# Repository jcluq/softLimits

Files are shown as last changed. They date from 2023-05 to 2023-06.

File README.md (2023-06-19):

# Elipses

Elipses are a series of kinetic sculptures which base their design on a string loop throwing contraption referred to as a string shooter. The mechanism consists of two motors rotating in opposite directions, which impulse a loop of yarn to a distance dependent on the speed of the motors and the length of the string. Because the string is looped, the yarn returns to the string shooter, getting fed again into the motors. This continuous throw generates a levitating elliptical shape. This phenomenon is quite interesting and eye-catching, as it produces a peculiar behavior that our perception is not used to experiencing.

## softLimits

On softLimits, 5 different nodes are located in the space close to eachother. Each node consists of a string shooter mounted on a servo motor to control the angle of throw. The servo motor is then mounted on top of a rotating platform controlled by a stepper motor. A slip ring is used to connect the servo motor and allow 360+ degrees of rotation without entangling the cables. All the motors are driven by a ESP32 based micro controller which rests on a custom PCB for handling all the copper circuitry.

The esp32 micro controller on each node allows them to do be controlled via Wi-Fi through OSC messages using UDP protocol. A custom software made in Processing acts as an interface for the nodes, allowing real time visualization of position and speed, as well as sending messages to them in order to change their parameters.

For the Soft Limits choreography, each node has a behaviour assigned to it. Behaviors are made up of 4 different parameters: throwing speed, rotation speed, rotation direction, and shooter angle. The nodes are then allowed to run on these parameters freely, until the software detects a collision between them. When this happens, a "swap" between parameters occurs, changing the shapes and movement of both nodes. When the 5 nodes are allowed to run freely and interact, an ever-changing play takes place.

## PoC (Process of Creation)

The creation of this artwork has meant a multidisciplinary research touching a number of different disciplines: wireless communications, mechanical design, digital fabrication, circuit and PCB design, welding, among many others. 

For the first string shooters I was basing myself on a design created by the user scorch on the page [Thingy verse](https://www.thingiverse.com/thing:3647986). This version was almost entirely made of laser cut parts, which even tho they where quick to produce, they were also very difficult to modify mainly because I didnt had the original archives that were used to design the devices. 

My next step was to create my own string shooter. For this I 3D modeled my own parts with the use of TICAD and start 3d printing the parts. This allowed me to test and modify specific parts and functions in a relative cheap and fast way. I changed the 5VDC motors I was using for faster and stronger 5-24V motors. The hardest obstacle I kept on finding was the lack of friction on the wheels which made contact with the yarn. On a [research](https://www.researchgate.net/publication/338578099_String_Shooter's_overall_shape_in_ambient_air) about the overall shapes of string shooters in air, the use of RC cars wheels was reported successful. After implementing these wheels on my design, I achieved a desired stability on my string shooters. 

For the tilt and pan module, I used a mg996r motor attached to a tilt metal bracket. Due to the screw fixtures on the bracket, setting up the string shooter on top of it was very easily done, by using threaded inserts on the 3d printed material. For the pan mechanism, I designed a tower structure to hold the bearings and the slip ring together, while giving enough space for the tilt mechanism to change angle without obstruction. For all this design process, fusion360 was very useful again as it allowed me to design with a modular a approach, having different parts which would then be "assembled" onto the final object. This modular approach proved to be a great constrain to prototyping because of the constant tests and modifications. 

For the electrical and communication design, I wanted to have a single line of power as the only physical input to each node. I used 12V as my main power and later used a LM1085 power regulator to send 5V to both my servomotor and micro controller. The ESP32 drive the 24VDC motors through an IRL540 mosfet, using PWM to change the throwing speed. The esp uses an A4988 driver in order to translate the stepper movements as well as to set up micro stepping. The mg996r motor is driven simply by a PWM output. 

The PCB was designed in KiCad and its shape and design was made to fit on the previous 3D models designed on Fusion360.

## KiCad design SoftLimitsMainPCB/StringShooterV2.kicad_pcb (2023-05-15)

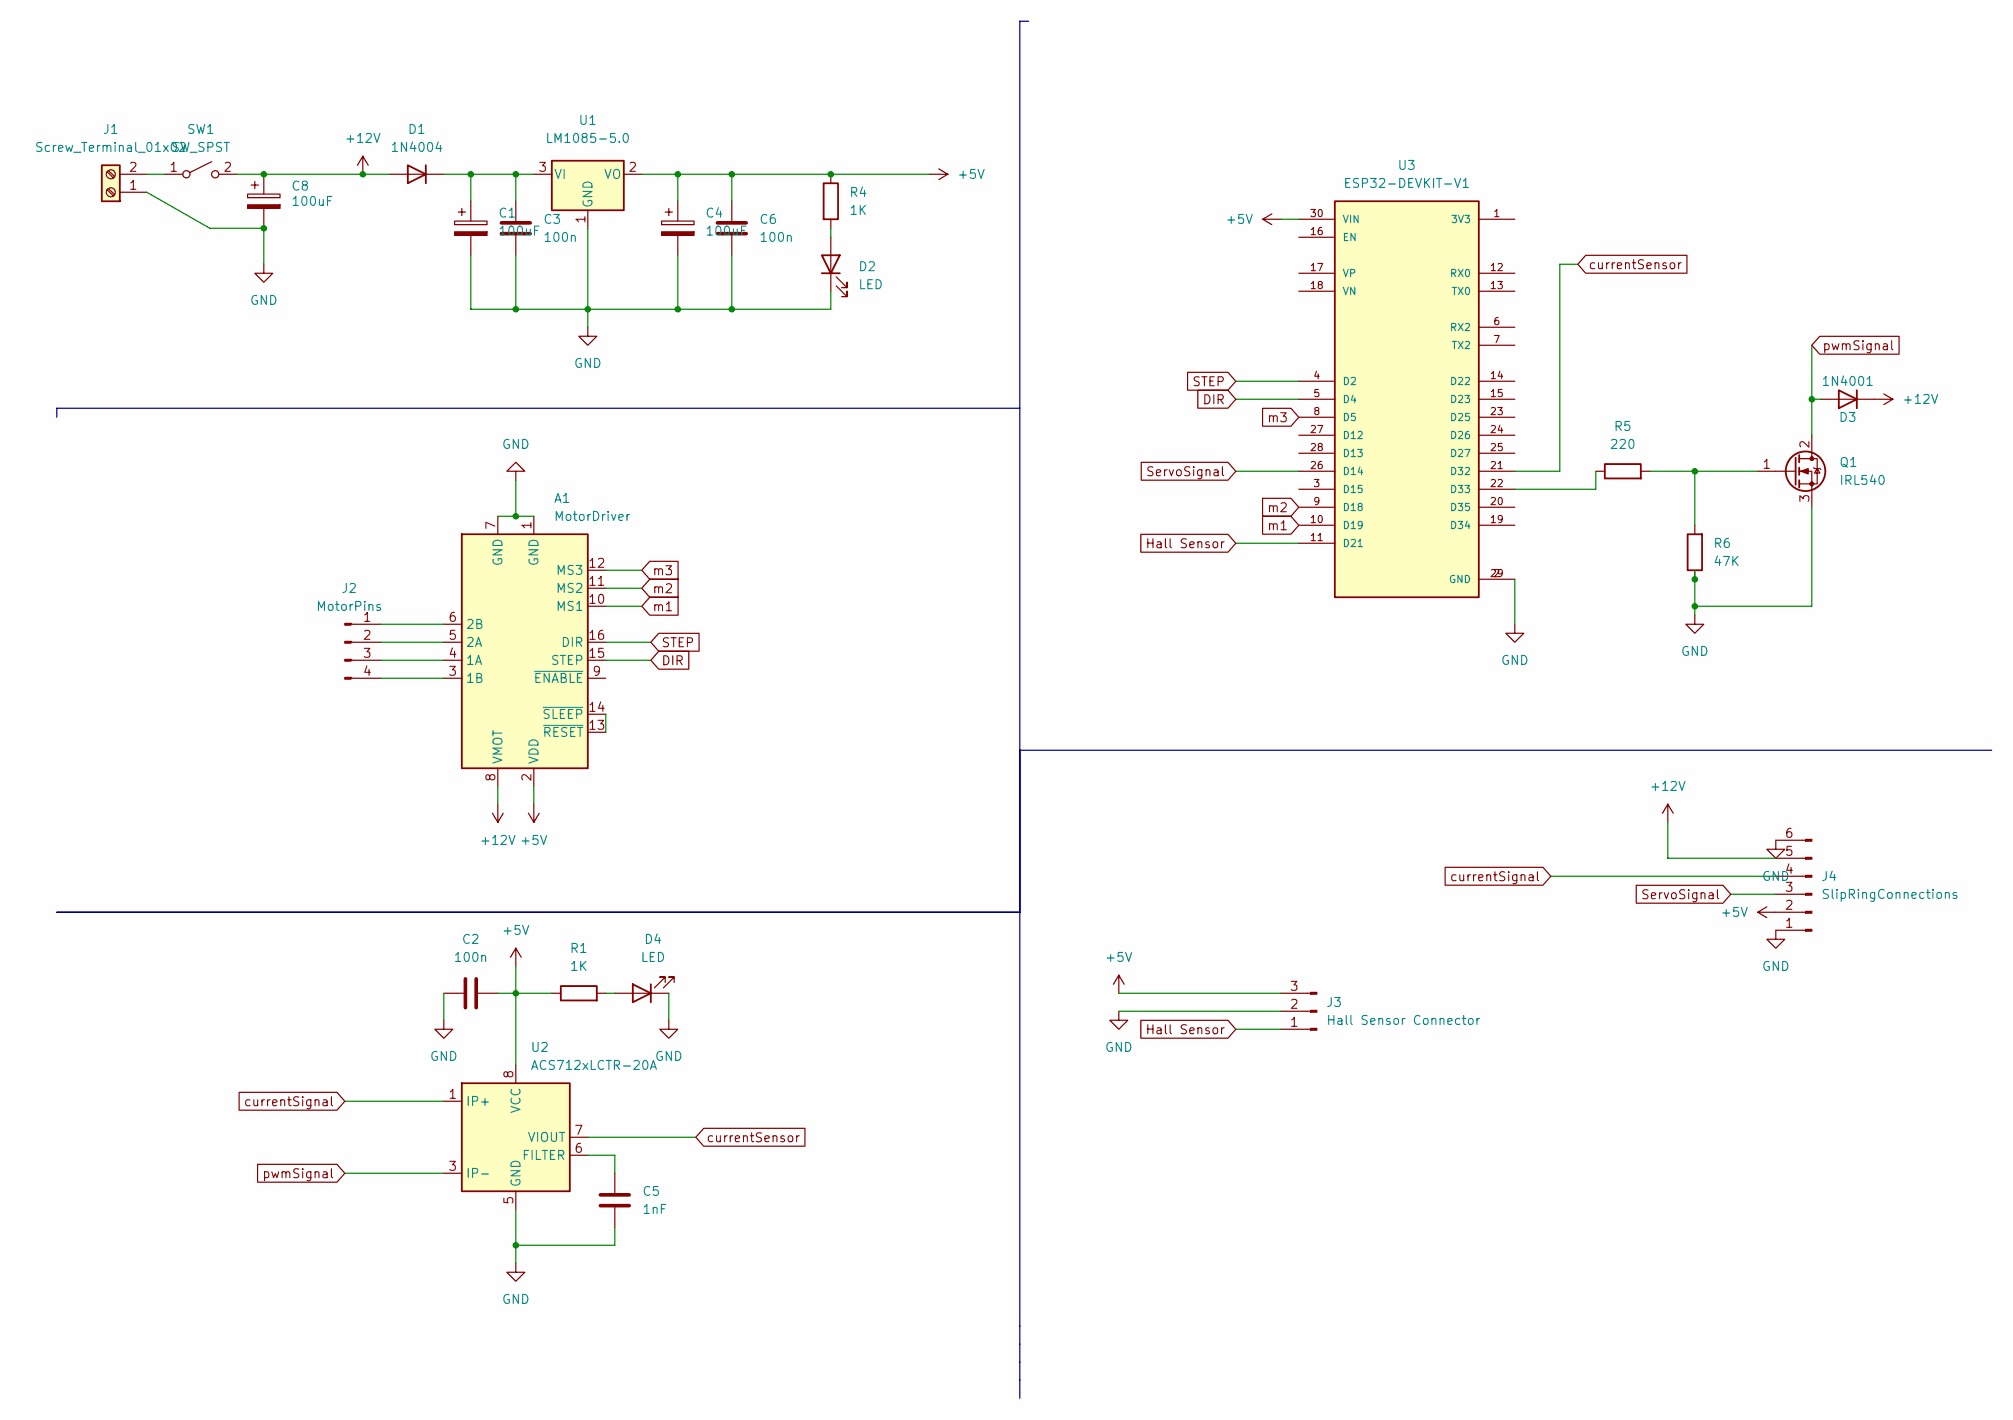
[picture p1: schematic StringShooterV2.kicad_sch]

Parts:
A1: MotorDriver; Pololu_Breakout-16_15.2x20.3mm
C1, C4, C8: 100uF; CP_Radial_D6.3mm_P2.50mm
C2, C3, C6: 100n; C_0805_2012Metric_Pad1.18x1.45mm_HandSolder
C5: 1nF; C_0805_2012Metric_Pad1.18x1.45mm_HandSolder
D1: 1N4004; D_SMA_Handsoldering
D2, D4: LED; D_0603_1608Metric_Pad1.05x0.95mm_HandSolder
D3: 1N4001; D_SMA_Handsoldering
J1: Screw_Terminal_01x02; TerminalBlock_bornier-2_P5.08mm
J2: MotorPins; PinSocket_1x04_P2.54mm_Vertical
J3: Hall Sensor Connector; PinSocket_1x03_P2.54mm_Vertical
J4: SlipRingConnections; PinSocket_1x06_P2.54mm_Vertical
Q1: IRL540; TO-220-3_Horizontal_TabDown
R1, R4: 1K; R_0805_2012Metric_Pad1.20x1.40mm_HandSolder
R5: 220; R_0805_2012Metric_Pad1.20x1.40mm_HandSolder
R6: 47K; R_0805_2012Metric_Pad1.20x1.40mm_HandSolder
SW1: SW_SPST; mts102
U1: LM1085-5.0; TO-263-3_TabPin2
U2: ACS712xLCTR-20A; SOIC-8_3.9x4.9mm_P1.27mm
U3: ESP32-DEVKIT-V1; MODULE_ESP32_DEVKIT_V1; PARTREV N/A

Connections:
+5V: A1.2 (VDD), C2.2, C4.1, C6.1, J3.3, J4.2, R1.1, R4.1, U1.2 (VO), U2.8 (VCC), U3.30 (VIN)
+12V: A1.8 (VMOT), C8.1, D1.2 (A), D3.1 (K), J4.5, SW1.2 (B)
DIR: A1.15 (STEP), U3.5 (D4)
GND: A1.1 (GND), A1.7 (GND), C1.2, C2.1, C3.2, C4.2, C5.2, C6.2, C8.2, D2.1 (K), D4.1 (K), J1.1, J3.2, J4.1, J4.6, Q1.3 (S), R6.1, U1.1 (GND), U2.5 (GND), U3.2 (GND), U3.29 (GND)
Hall Sensor: J3.1, U3.11 (D21)
unnamed: A1.3 (1B), J2.4
unnamed: A1.4 (1A), J2.3
unnamed: A1.5 (2A), J2.2
unnamed: A1.6 (2B), J2.1
unnamed: A1.13 (~RESET), A1.14 (~SLEEP)
unnamed: C1.1, C3.1, D1.1 (K), U1.3 (VI)
unnamed: C5.1, U2.6 (FILTER)
unnamed: D2.2 (A), R4.2
unnamed: D4.2 (A), R1.2
unnamed: J1.2, SW1.1 (A)
unnamed: Q1.1 (G), R5.2, R6.2
unnamed: R5.1, U3.22 (D33)
STEP: A1.16 (DIR), U3.4 (D2)
ServoSignal: J4.3, U3.26 (D14)
currentSensor: U2.7 (VIOUT), U3.21 (D32)
currentSignal: J4.4, U2.1 (IP+), U2.2 (IP+)
m1: A1.10 (MS1), U3.10 (D19)
m2: A1.11 (MS2), U3.9 (D18)
m3: A1.12 (MS3), U3.8 (D5)
pwmSignal: D3.2 (A), Q1.2 (D), U2.3 (IP-), U2.4 (IP-)

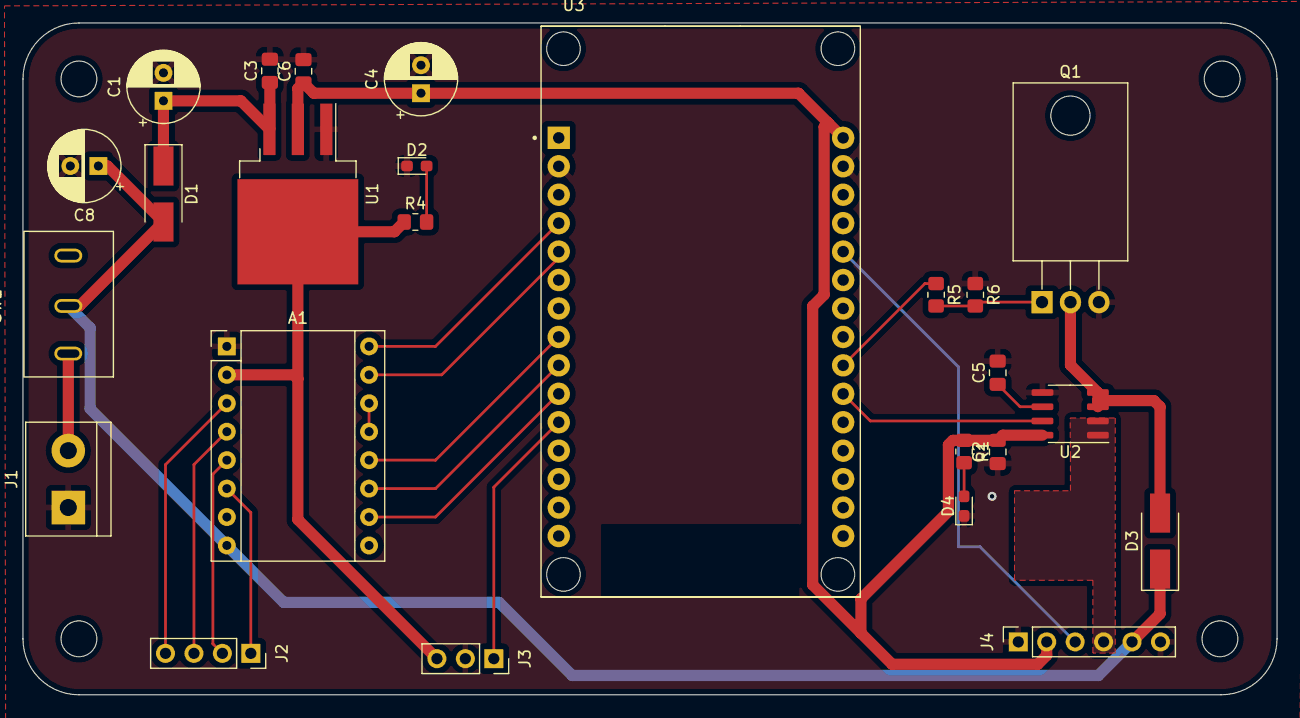
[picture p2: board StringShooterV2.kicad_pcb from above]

Board: 2 copper layers, 112.0 x 60.0 mm, 25 parts (0 on the bottom side), 25 nets.

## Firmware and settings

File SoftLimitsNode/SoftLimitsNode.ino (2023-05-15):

/*
   StringNode
    
   Code based in ralfs beacker boilerplate  
   https://github.com/rlfbckr/simple-node

*/

#include <ESP32Servo.h>
#include <WiFi.h>
#include <WiFiMulti.h>
#include <HTTPClient.h>
#include <HTTPUpdate.h>
#include "AsyncUDP.h"
#include "Shooter.h"


#include <Chrono.h>
#include <OSCBundle.h>
#include <EEPROM.h>
#include <AccelStepper.h>

#define EEPROM_SIZE 12
#define DIR_PIN 2
#define STEP_PIN 4
#define SH_PIN 33
#define M1_PIN 19
#define M2_PIN 18
#define M3_PIN 5
#define HOME_PIN 21
#define SERVO_PIN 14
#define CUR_PIN 32


int MY_NODE_ID = -1;

float FW_VERSION = 0.17; /// increment for next upload



//const char DEFAULT_URL_FW_VERSION[] = "http://192.168.0.113:8080/release/version.txt";
//const char  DEFAULT_URL_FW_BINARY[] = "http://192.168.0.113:8080/release/firmware.bin";

const char DEFAULT_URL_FW_VERSION[] = "http://192.168.4.100:8080/release/version.txt";
const char  DEFAULT_URL_FW_BINARY[] = "http://192.168.4.100:8080/release/firmware.bin";

boolean LOCK_UDP_REICEIVER = false; // lock UDP/OSC receiver to avoid shit while flashing a new firmware
char URL_FW_VERSION[512];
char URL_FW_BINARY[512];
boolean UPDATE_FIRMWARE = false; // hook in firmwareupdate

long pingInterval = 5; // every 2 seconds
int networkLocalPort = 8888;
int networkOutPort = 9999; // remote port to receive OSC

int stepNum = 500;
int microStep = 16;
int jogVal = 2000000;
int stepperSpeed = 10 * microStep;
int stepperDirection = 1;
int stepperRealPosition;

boolean HALL_SENSOR = false;
boolean isJogging = false;
int shooterSpeed = 450;

boolean HOMING = false;
boolean homingSet = false;
boolean stopper = false;



WiFiMulti wifiMulti;
Chrono pingTimer;
AsyncUDP udp;
AsyncUDP udpOut;
AccelStepper stepper(AccelStepper::DRIVER, STEP_PIN, DIR_PIN);
Servo servo;
Shooter shooter(SH_PIN);

void setup() {
  strncpy(URL_FW_VERSION, DEFAULT_URL_FW_VERSION, strlen(DEFAULT_URL_FW_VERSION));
  strncpy(URL_FW_BINARY, DEFAULT_URL_FW_BINARY, strlen(DEFAULT_URL_FW_BINARY));
  MY_NODE_ID = readNodeIDfromEEPROM();
  Serial.begin(115200);
  Serial.print("--> NODE  v:");
  Serial.println(FW_VERSION);
  initWIFI();
  initUDP();
  microStepSetup();
  
  servo.attach(SERVO_PIN);
  stepper.setMaxSpeed(1500);
  stepper.setCurrentPosition(0);
  stepper.setSpeed(stepperSpeed* stepperDirection*microStep);
  stepper.stop();

  servo.write(90);
  beginHomming();
  
}

void loop() {
  Serial.println(digitalRead(HOME_PIN));
  if (UPDATE_FIRMWARE) {
    if (getFirmwareVersionFromServer()) { // check if a new version is avaiable on the server
      updateFirmwareFromServer(); // get binary and flash it.
    }
    UPDATE_FIRMWARE = false; // update done
  }

  if (pingTimer.hasPassed(pingInterval)) {
    pingTimer.restart();
    sendPingOSC();
  }

  if (HOMING) {
    homingSequence();
      
    }
    
    


 // Serial.println(digitalRead(HOME_PIN));
 if(stopper){
  stepper.stop();
 }
 else {
  stepper.runSpeedToPosition();
 }
 //currentMeasurement();
  stepperRealPosition = (((stepper.currentPosition()/microStep)%stepNum)+stepNum)%stepNum;
  //stepper.setCurrentPosition(stepperRealPosition);
  shooter.runShooter(shooterSpeed);
  //Serial.println(((stepper.currentPosition()%stepNum)+stepNum)%stepNum);
}

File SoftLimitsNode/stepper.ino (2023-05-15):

void microStepSetup()
{
  pinMode(M1_PIN,OUTPUT);
  pinMode(M2_PIN,OUTPUT);
  pinMode(M3_PIN,OUTPUT);

  digitalWrite(M1_PIN,HIGH);
  digitalWrite(M2_PIN,HIGH);
  digitalWrite(M3_PIN,HIGH);
}




void changeStepperDirection(int dir) {
  stopper = false;
  stepper.stop();
  stepperDirection = dir;
  stepper.moveTo(jogVal * stepperDirection*microStep);
  stepper.setSpeed(stepperSpeed * stepperDirection*microStep);
  Serial.println(stepperDirection);
}

void beginHomming(){
  HOMING = true;
  homingSet=false;
}

void homingSequence() {
  stopper = false;
   
  if (!homingSet) {
    stepper.stop();
    stepperDirection = 1;
    stepper.moveTo(jogVal * stepperDirection);
    stepper.setSpeed(10*microStep * stepperDirection);
    LOCK_UDP_REICEIVER = true;
    homingSet = true;
  }
  if (digitalRead(HOME_PIN)==0) {
    stepper.stop();
    stepper.setCurrentPosition(0);
    HOMING = false;
    homingSet = false;
    stepper.setSpeed(stepperSpeed * stepperDirection*microStep);
    LOCK_UDP_REICEIVER = false;
    //jog();
  }
} 

void jog() {
  stopper = false;
  stepper.stop();
  stepper.moveTo(jogVal * stepperDirection);
  stepper.setSpeed(stepperSpeed * stepperDirection*microStep);
  isJogging = true;
}

void goTo(int pos) {
  stopper = false;
  pos = pos*microStep;
  stepper.setCurrentPosition(stepperRealPosition*microStep);
  if (pos > stepper.currentPosition()) {
    if ((stepper.currentPosition() + stepNum - pos) < (pos - stepper.currentPosition())) {
      stepper.stop();
      stepperDirection = -1;
      stepper.moveTo(pos - stepNum - 1 );
      stepper.setSpeed(stepperSpeed * stepperDirection*microStep);
    }  else {
      stepper.stop();
      stepperDirection = 1;
      stepper.moveTo(pos);
      stepper.setSpeed(stepperSpeed * stepperDirection*microStep);

    }
  }
    else {
      if ((stepNum + pos - stepper.currentPosition()) < (stepper.currentPosition() - pos)) {
        stepper.stop();
        stepperDirection = +1;
        stepper.moveTo(pos + stepNum - 1);
        stepper.setSpeed(stepperSpeed * stepperDirection*microStep);
      }  else {
        stepper.stop();
        stepperDirection = -1;
        stepper.moveTo(pos);
        stepper.setSpeed(stepperSpeed * stepperDirection*microStep);
      }
    }

    
    isJogging = false;
  }

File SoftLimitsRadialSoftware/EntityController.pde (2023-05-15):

class EntityController {
  int id;
  float value;
  int shootingSpeed = 400;
  controlP5.Group group;
  int relSize;
  
  controlP5.Slider shooterSlider;
  controlP5.Toggle stepperToggle;
  controlP5.Knob stepperKnob;
  controlP5.Slider servoSlider;
  controlP5.Slider stepperSpeedSlider;
  
  int stepperValue;
  int servoAngle;
  boolean manualPos = false;
  Entity entity;




  EntityController(Entity ent, int iden ) {
    entity = ent;
    id = iden;
    relSize=5;

    group = cp5
      .addGroup("Node"+id)
      .setWidth(500)
      .open()
      .setBarHeight(20)
      .setCaptionLabel("node "+id)
      //.setColorBackground(color(120))
      .setColorForeground(color(120))
      ;

    group.getCaptionLabel().align(ControlP5.CENTER, ControlP5.CENTER);


       stepperToggle = cp5.addToggle("stepperToggle"+id)
      .setPosition(40, 135)
      .setLabelVisible(false)
      .plugTo(this, "manualPos")
      .moveTo(group);




    shooterSlider = cp5.addSlider("shootingSpeed"+id)
      .setPosition(120, 10)
      .moveTo(group)
      .setWidth(relSize*50)
      .setHeight(relSize*5)
      .setMin(360)
      .setMax(600)
      .plugTo(this, "shootingSpeed")
      .setLabel("ShootingSpeed");
      
    servoSlider = cp5.addSlider("servoAngle"+id)
      .setPosition(120, 40)
      .moveTo(group)
      .setWidth(relSize*50)
      .setHeight(relSize*5)
      .setMin(45)
      .setMax(110)
      .plugTo(this, "servoAngle")
      .setLabel("servoAngle");
      
      stepperSpeedSlider = cp5.addSlider("stepperSpeed"+id)
      .setPosition(120, 70)
      .moveTo(group)
      .setWidth(relSize*50)
      .setHeight(relSize*5)
      .setMin(0)
      .setMax(50)
      .plugTo(this, "stepperSpeed")
      .setLabel("stepperSpeed");

    stepperKnob =  cp5.addKnob("positionKnob"+id)
      .setViewStyle(2)
      .plugTo(this, "stepperValue")
      .setPosition(10, 10)
      .setSize(100, 100)
      .setRange(0, 500)
      .setAngleRange(6.2831853072)
      .setStartAngle(1.57079)
      .setColorBackground(color(100,100))
      .moveTo(group)
      .setLabel("stepper")
      .setConstrained(false)
      .setDecimalPrecision(1)
      .lock()
      .setId(id)
      ;

    
    
    
    
    stepperToggle.addCallback(new CallbackListener() {
      public void controlEvent(CallbackEvent theEvent) {
        if (theEvent.getAction()==ControlP5.ACTION_BROADCAST) {
          stepperKnob.setLock(!manualPos);
         
          if(stepperKnob.isLock()){
          stepperKnob.setColorBackground(color(100,100));
          entity.jog();
          }
          else{
          stepperKnob.setColorBackground(cp5.getColor().getBackground());
          entity.stopRotation();
          }
        }
      }
    });




    nodeControls.addItem(group);
  }
}
